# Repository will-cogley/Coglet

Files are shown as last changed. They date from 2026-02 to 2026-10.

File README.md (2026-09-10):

# Coglet
Will Cogley's DIY Desktop Companion for Makers. Support our kickstarter to allow us to keep improving Coglet and so we can offer all components in one place! https://www.kickstarter.com/projects/willcogley/coglet-open-source-3d-printable-robot-companion-kit

# Instructions
*Core documentation for the system and PCB can be found in the [CogNog Datasheet](https://github.com/will-cogley/Coglet/blob/main/CogNogDatasheet.md)*

Refer to the [build video](https://www.youtube.com/watch?v=-7I-jFSNP2E). 

For further reading and troubleshooting, refer to the translated docs in this repo.

# Parts List
Consider backing our [kickstarter](https://www.kickstarter.com/projects/willcogley/coglet-open-source-3d-printable-robot-companion-kit) so we can provide all the parts in [one place!](https://nmrobots.com/)
- CogNog PCB - See project files
- [Grove Vision AI V2 plus camera and adaptor](https://nmrobots.com/products/grove-vision-ai-module-v2-hd-camera-adaptor-15-pin-flex-cable)
- [Microphone](https://www.amazon.co.uk/EC-Buying-INMP441-Omnidirectional-Microphone/dp/B0C1C64R8S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)
- [6 Pin PicoBlade Connector](https://thepihut.com/products/1-25mm-pitch-6-pin-cable-20cm-long-1-1-cable-molex-picoblade-compatible)
- [Speaker](https://www.aliexpress.com/item/1005008267342362.html?spm=a2g0o.order_list.order_list_main.5.2c9d1802tZvBqq)
- USB input to JST XH (3A recommended)
- [ESP Camera - OV3660](https://www.aliexpress.com/item/1005007456084280.html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)
- [ESP Cam Ribbon Cable](https://www.digikey.co.uk/en/products/detail/gct/05-24-A-0152-A-4-06-4-T/21266890)
- [ESP Cam Adaptor](https://www.digikey.co.uk/en/products/detail/adafruit-industries-llc/4524/12323567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)
- [9x Servos - These are tight, MG90s may also work](https://uk.robotshop.com/products/kpower-9g-analog-metal-gear-rc-servo-m0090)
- [Realistic Camera-Compatible Eyes](https://nmrobots.com/products/ultra-realistic-eyeball-compatible-with-face-tracking-eyemech-%CE%B53-4)

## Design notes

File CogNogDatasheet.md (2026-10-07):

# 1. Hardware

## 1.1 Description

A dual-MCU animatronics and AI processing platform combining an ESP32-S3 for machine learning/vision/audio and an RP2040 for real-time kinematics and servo control.

### 1.1.1 Key Features

- **Main Processor:** ESP32-S3 (Wi-Fi/BLE, AI acceleration, I/O)
- **Coprocessor:** RP2040 (Real-time I/O, motion profiling)
- **Motor Control:** PCA9685 16-channel PWM driver
- **Vision:** DVP Camera interface (supports GC0308)
- **Audio:** I2S Microphone input and I2S Speaker amplifier
- **Power:** Single USB-C power input for up to 12 servos

---

## 2. System Block Diagram



---

## 3. Pinout



### 3.1 Default Servo Wiring

| Named Servo | Key in Code | Socket Number (Also PCA9685 Pin No.) |
| --- | --- | --- |
| Right Ear | "EAR" | 0 |
| Left Ear | "EAL" | 1 |
| Eyelid | "LID" | 2 |
| Mouth | "MOU" | 3 |
| Right Eye | "EYR" | 5 |
| Left Eye | "EYL" | 4 |
| Neck Pitch | "PIT" | 8 |
| Neck Roll | "ROL" | 9 |
| Base Yaw | "YAW" | 10 |

---

## 4. Components

### 4.1 On-Board Components

| Name | Function | Interface | Datasheet |
| --- | --- | --- | --- |
| ESP32-S3 | Wi-Fi/BLE, AI acceleration, I/O | - | https://documentation.espressif.com/esp32-s3_datasheet_en.pdf |
| RP2040 | Real-time I/O, motion profiling | - | https://pip-assets.raspberrypi.com/categories/814-rp2040/documents/RP-008371-DS-1-rp2040-datasheet.pdf |
| MAX98357A | Speaker amplifier | I2S | https://cdn-shop.adafruit.com/product-files/3006/MAX98357A-MAX98357B.pdf |
| PCA9685 | Servo driver | I2C | https://www.futurlec.com/Philips/PCA9685PW.shtml |
| CH343P | USB bus converter chip | UART | https://cdn-learn.adafruit.com/assets/assets/000/134/549/original/CH343DS1.PDF?1737477957 |

### 4.2 Recommended External Components

| Name | Function | Interface | Datasheet | Link | Notes |
| --- | --- | --- | --- | --- | --- |
| GC0308 Camera | In-depth vision processing | DVP | https://download.kamami.pl/p1197045-GC0308.pdf | - | **Coglet uses a customised camera with inverted pin layout!** |
| Grove Vision AI Module | Processes face tracking  | UART | https://wiki.seeedstudio.com/Grove-Vision-AI-Module/ | https://nmrobots.com/products/grove-vision-ai-module-v2-hd-camera-adaptor-15-pin-flex-cable |  |
| OV5647 Camera | Realtime face tracking | DVP | - | https://nmrobots.com/products/grove-vision-ai-module-v2-hd-camera-adaptor-15-pin-flex-cable |  |
| Speaker | Speaking responses out loud | Direct Voltage | - | - |  |
| Microphone | Recording audio, listening for responses | I2S | - | - |  |
| Servos | Driving the robot | PWM | - | https://nmrobots.com/products/tiankongrc-ts90md-micro-servo-motor-with-metal-gears |  |

## 5. Power Ratings

*Stresses beyond these limits may cause permanent damage to the board.* 

| Parameter | Symbol | Typical Voltage $V$ | Typical Current $A$ |
| --- | --- | --- | --- |
| **Main Input** | **$V_{IN}$** | **5.0** | **3.0** |
| ESP32 Logic Input  | $V_{LOGIC\_ESP}$ | 3.3 | 0.04 |
| RP2040Logic Input  | $V_{LOGIC\_RP}$ | 3.3 | 0.012 |
| Servo Output Voltage | $V_{IN\_SERVO}$ | 5.0 | 3.0 |

---

## 6. Dual-MCU Communication Protocol

ESP32-s3 sends commands to the RP2040 via UART in the form of simple strings which correspond to preset animations:

$ESP-RX_{GPIO18} : RP2040-TX1_{GPIO04}$

$ESP-TX_{GPIO17} : RP2040-RX1_{GPIO05}$

---

## 7. Power Architecture

Power is provided to the board via the connector in the bottom left corner using a JST-XH connector. This input powers both MCUs via 3V3 LDOs, and the servos via an isolated 5V line. 

**It is required to use a 5V-3A rated power supply**(eg - a USB charger with 5V-3A power rating). If using the Coglet USB > JST XH adaptor, must use a USBA > USBC cable. 

The system can be powered via the programming port, but no power will be delivered to the servos (this approach can be helpful when debugging/developing on the ESP32)

---

## 8. Mechanical Specifications

- **Dimensions:** 72 mm x 81 mm
- **Mounting Holes:** 4 x 2.75mm (to suit M2.5 screws)
- **PCB Layers:** 4



---

## 9. Downloads

*Refer to GitHub root for open-source files such as schematic, layout, STEP, etc*

---

# 2. Software & Firmware

### 2.1 Overview

- Toolchain: ESP-IDF, C++, Python
- Key Libraries: XiaoZhi AI Open-Source Chatbot: https://github.com/78/xiaozhi-esp32

*FAQ: Is it essential to use XiaoZhi AI?  The system is a helpful starting point to get up and running quickly, but for developers it is not necessary. NMRobotics is also developing a locally-running alternative dashboard.* 

## 2.2 Default Functionality

| Item | Functionality |
| --- | --- |
| Programming Selector Switch | Use to switch which MCU is connected to the programming port USB - enabling you to program both MCUs with the same port |
| Calibration Mode Switch | Via the RP2040, put all servos into a default position to assist with making sure all servos are properly calibrated when assembling |
| Facetrack Mode Switch | Via the Grove Vision AI Board, track and follow user’s face in realtime (uses on-board local processing) |
| Servo Test Button  | Via the RP2040, simultaneously wiggle all servos back and forth by a few degrees to check ROM and function during assembly/testing |

## 2.3 Guides

*This section is a stub ! Most recent tutorial overview can be found here:*

https://youtu.be/-7I-jFSNP2E?si=6lqtyZIJ3J-2O9Dj

### 2.3.1 Manually Uploading Code

1. It is recommended to follow this guide to setup ESP-IDF: https://github.com/will-cogley/Coglet/blob/main/Translated Docs for XiaoZhi AI/Setting up the ESP IDF 5.5.2 Development Environment on Windows and Compiling Xiaozhi - Feishu Docs.pdf
2. Clone the github repository 
3. Using ESP-IDF, build and flash 

### 2.3.2 Adding a customised wakeword

1. coming soon

---

# 3. Troubleshooting

| Issue | Recommended action |
| --- | --- |
| "Images taken with camera are over/under exposed | Search in "main\boards\common\ esp32_camera. cc " for: {0xd3, 0xb0} Then change it to: {0xd3, 0x70}, If you think the light is too dim, change "0x70" to "0x78". Re-build and flash the code via ESP-IDF" |
| No power to main board when using USBC > JST XH adaptor board | Use a power adaptor featuring a USBA > USBC cable |

---

# 4. Revision History

| Revision | Date | Description | Author |
| --- | --- | --- | --- |
| V1.0 | 2025-12-02 | Initial prototype  | Will Cogley |
| V1.1 | 2026-01-07 | Minor tweaks  | Will Cogley |
| V2.0 | 2026-06-01 | First Production Prototype | Spike |
| V2.1 | 2026-07-02 | Alternative Production Prototype | Petr Dvorak |
| V2.2 | 2026-08-01 | Minor tweaks from Petr’s design | Xiao Zou |
| V3.0 | 2026-09-06 | Finalised production design for batch 01 | Xiao Zou, Will Cogley |

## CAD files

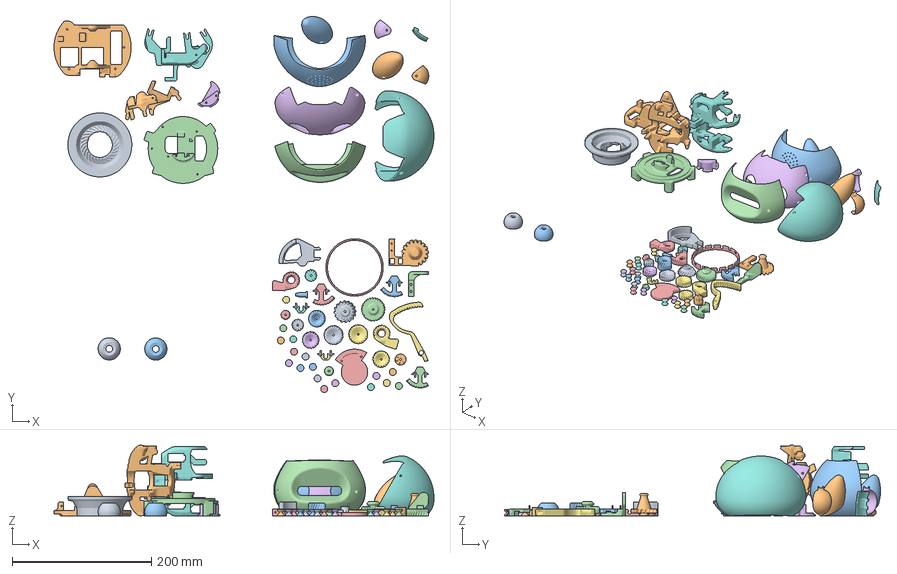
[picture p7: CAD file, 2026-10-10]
3D Printing Files/CogletC0_6_4.3mf
546.3 x 540.6 x 101.7 mm
Full.stl_32 x 2
Full (5).stl_1
Full (5).stl_2
Full.stl_35
Full.stl_48
Full.stl_58
Full.stl_20
Full.stl_8
Full.stl_19
Full.stl_31
Exterior - Eyelid.stl
Full.stl_26 x 2
Full.stl_30
Full.stl_38
Full.stl_16
Full.stl_65
Full.stl_64
Full.stl_29
Full.stl_25
Full - BottomPlug.stl
Full.stl_18
Full.stl_7
Full.stl_22
Full - Part 24.stl
Full.stl_9
Full - BodyMiddlePlatform.stl
Full (4).stl_1
Full.stl_53
Full.stl_57
Full (3).stl_2
Full (3).stl_1
Full.stl_2
Full.stl_24
HeadMech - EarLock.stl x 2
Full.stl_10 x 17
Full - EyeAdaptorR.stl x 2
Full - Foot (1).stl
Full - BodyTopPlatform (4).stl
Full (6).stl_1
Full (6).stl_2

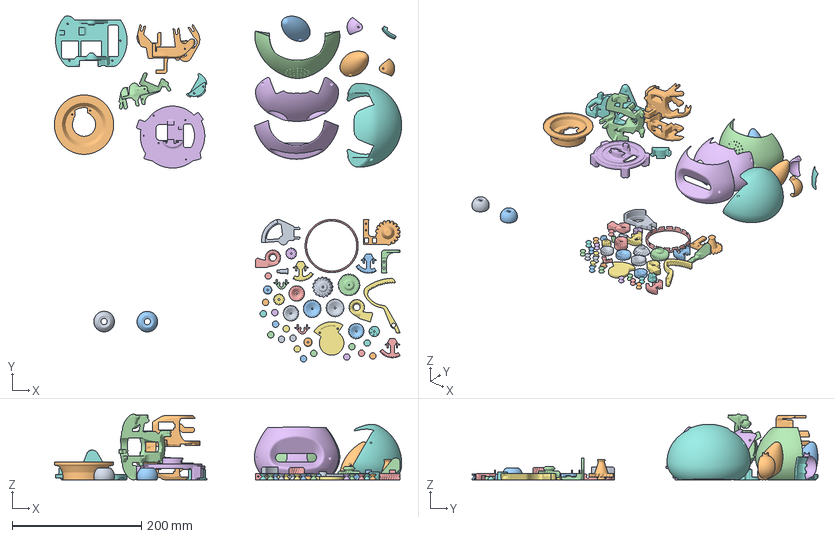
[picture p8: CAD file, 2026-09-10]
3D Printing Files/CogletC0_4.3mf
538.3 x 536.3 x 101.7 mm
Full.stl_32 x 2
Full (5).stl_1
Full (5).stl_2
Full.stl_35
Full.stl_48
Full.stl_58
Full.stl_20
Full.stl_8
Full.stl_19
Full.stl_31
Exterior - Eyelid.stl
Full.stl_26 x 2
Full.stl_30
Full.stl_38
Full.stl_16
Full.stl_65
Full.stl_64
Full.stl_52
Full.stl_29
Full.stl_45
Full.stl_25
Full - BottomPlug.stl
Full.stl_18
Full.stl_7
Full.stl_22
Full - Part 24.stl
Full.stl_9
Full - BodyMiddlePlatform.stl
Full (4).stl_1
Full - BodyTopPlatform.stl
Full.stl_53
Full - Foot.stl
Full.stl_57
Full.stl_47
Full.stl_44
Full (3).stl_2
Full (3).stl_1
Full.stl_2
Full.stl_24
HeadMech - EarLock.stl x 2
Full.stl_10 x 17

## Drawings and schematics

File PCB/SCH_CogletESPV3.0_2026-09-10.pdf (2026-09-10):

# ESP32-S3 N16R8

# Key

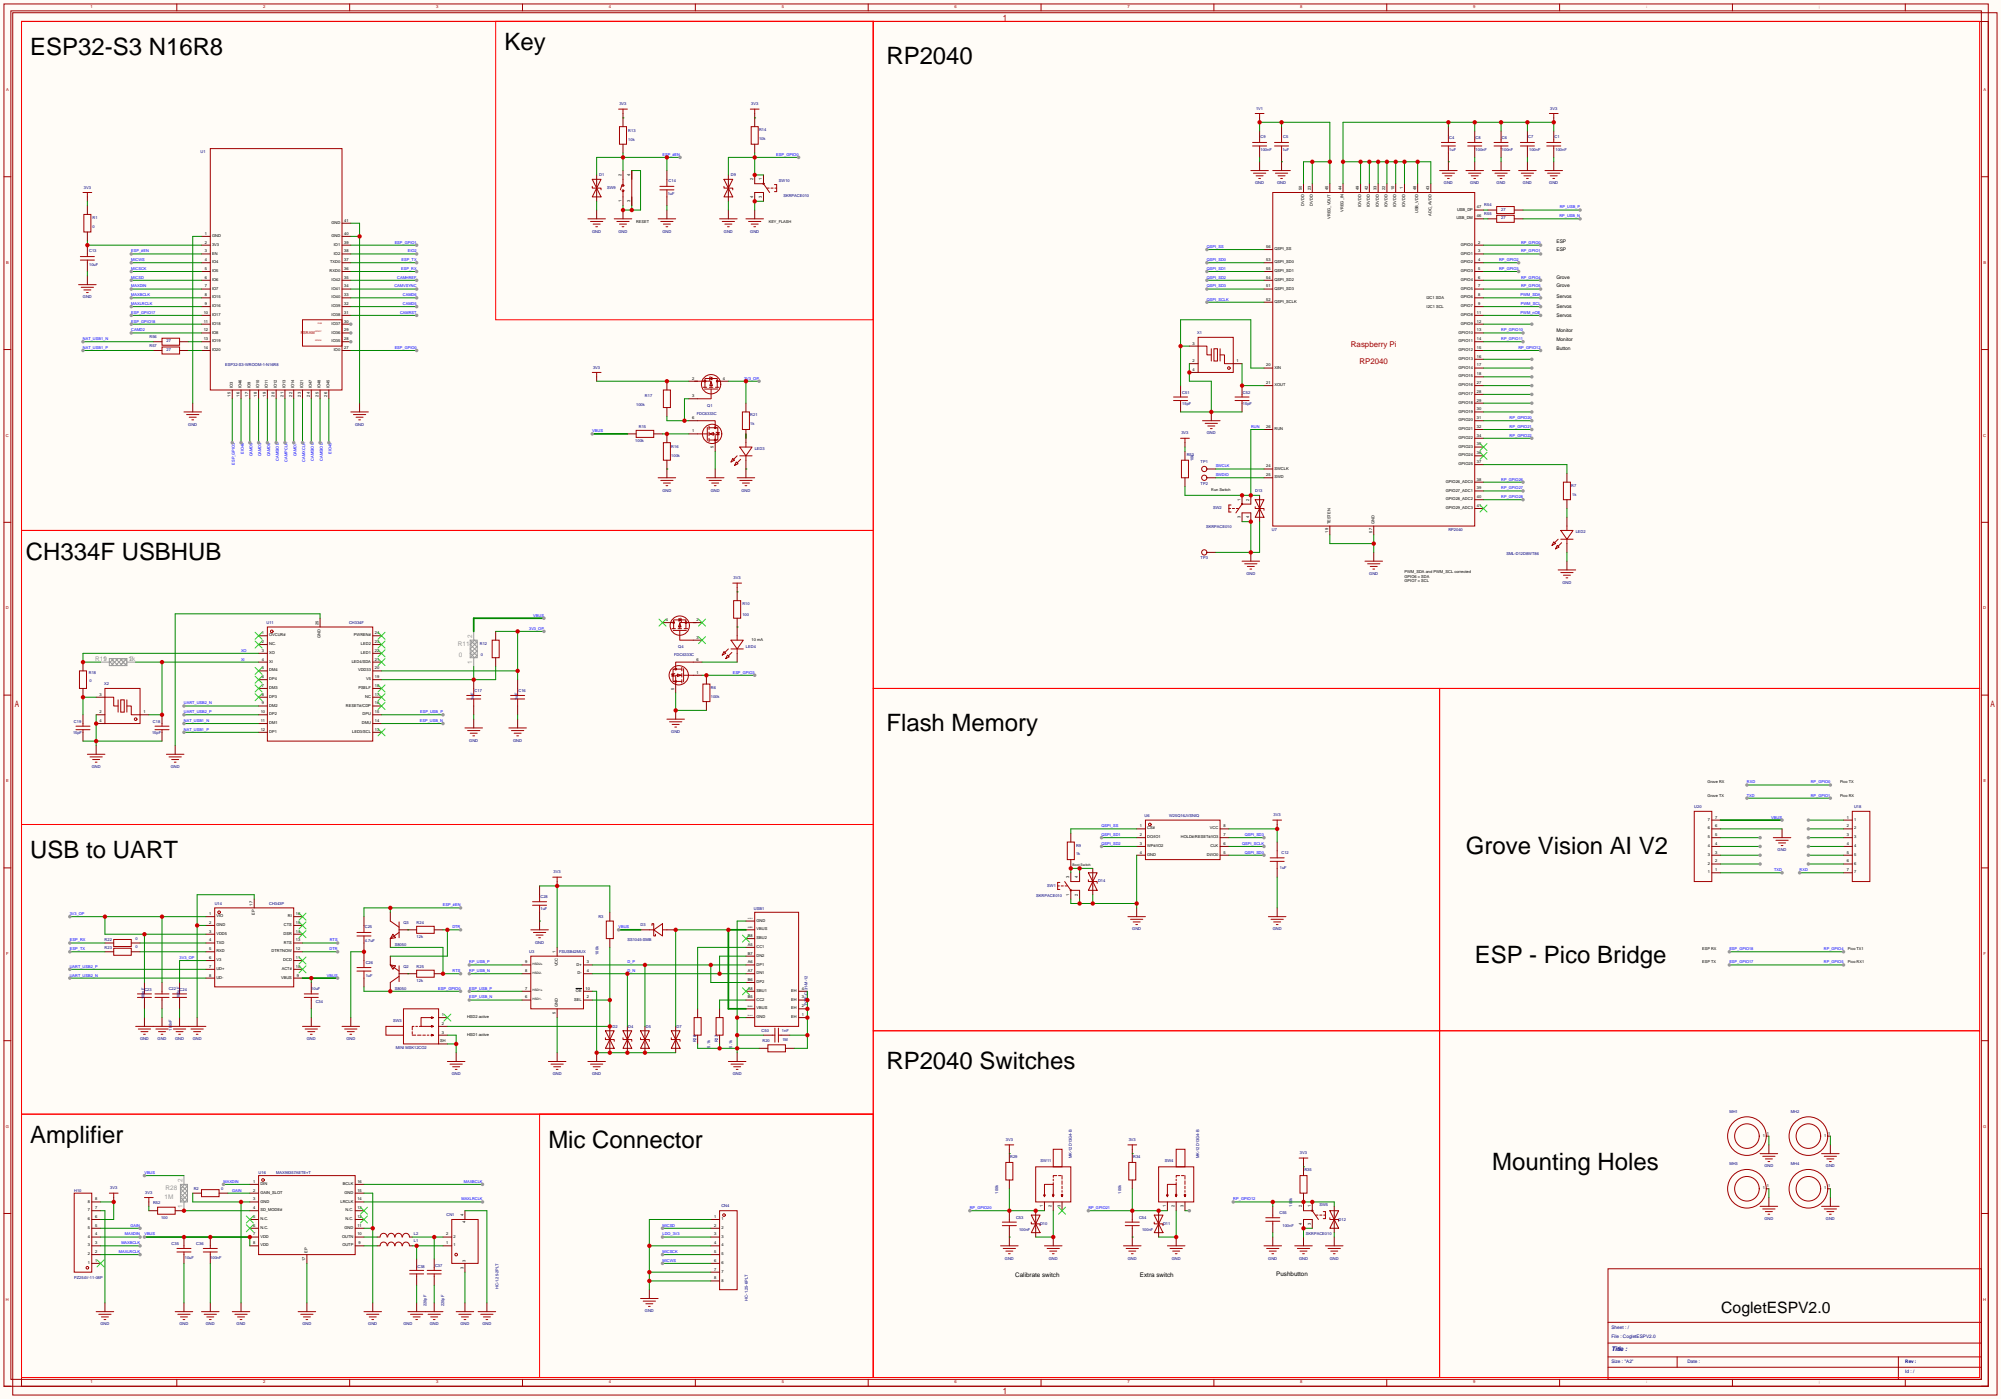
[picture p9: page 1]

Main Power | 3V3 LDO

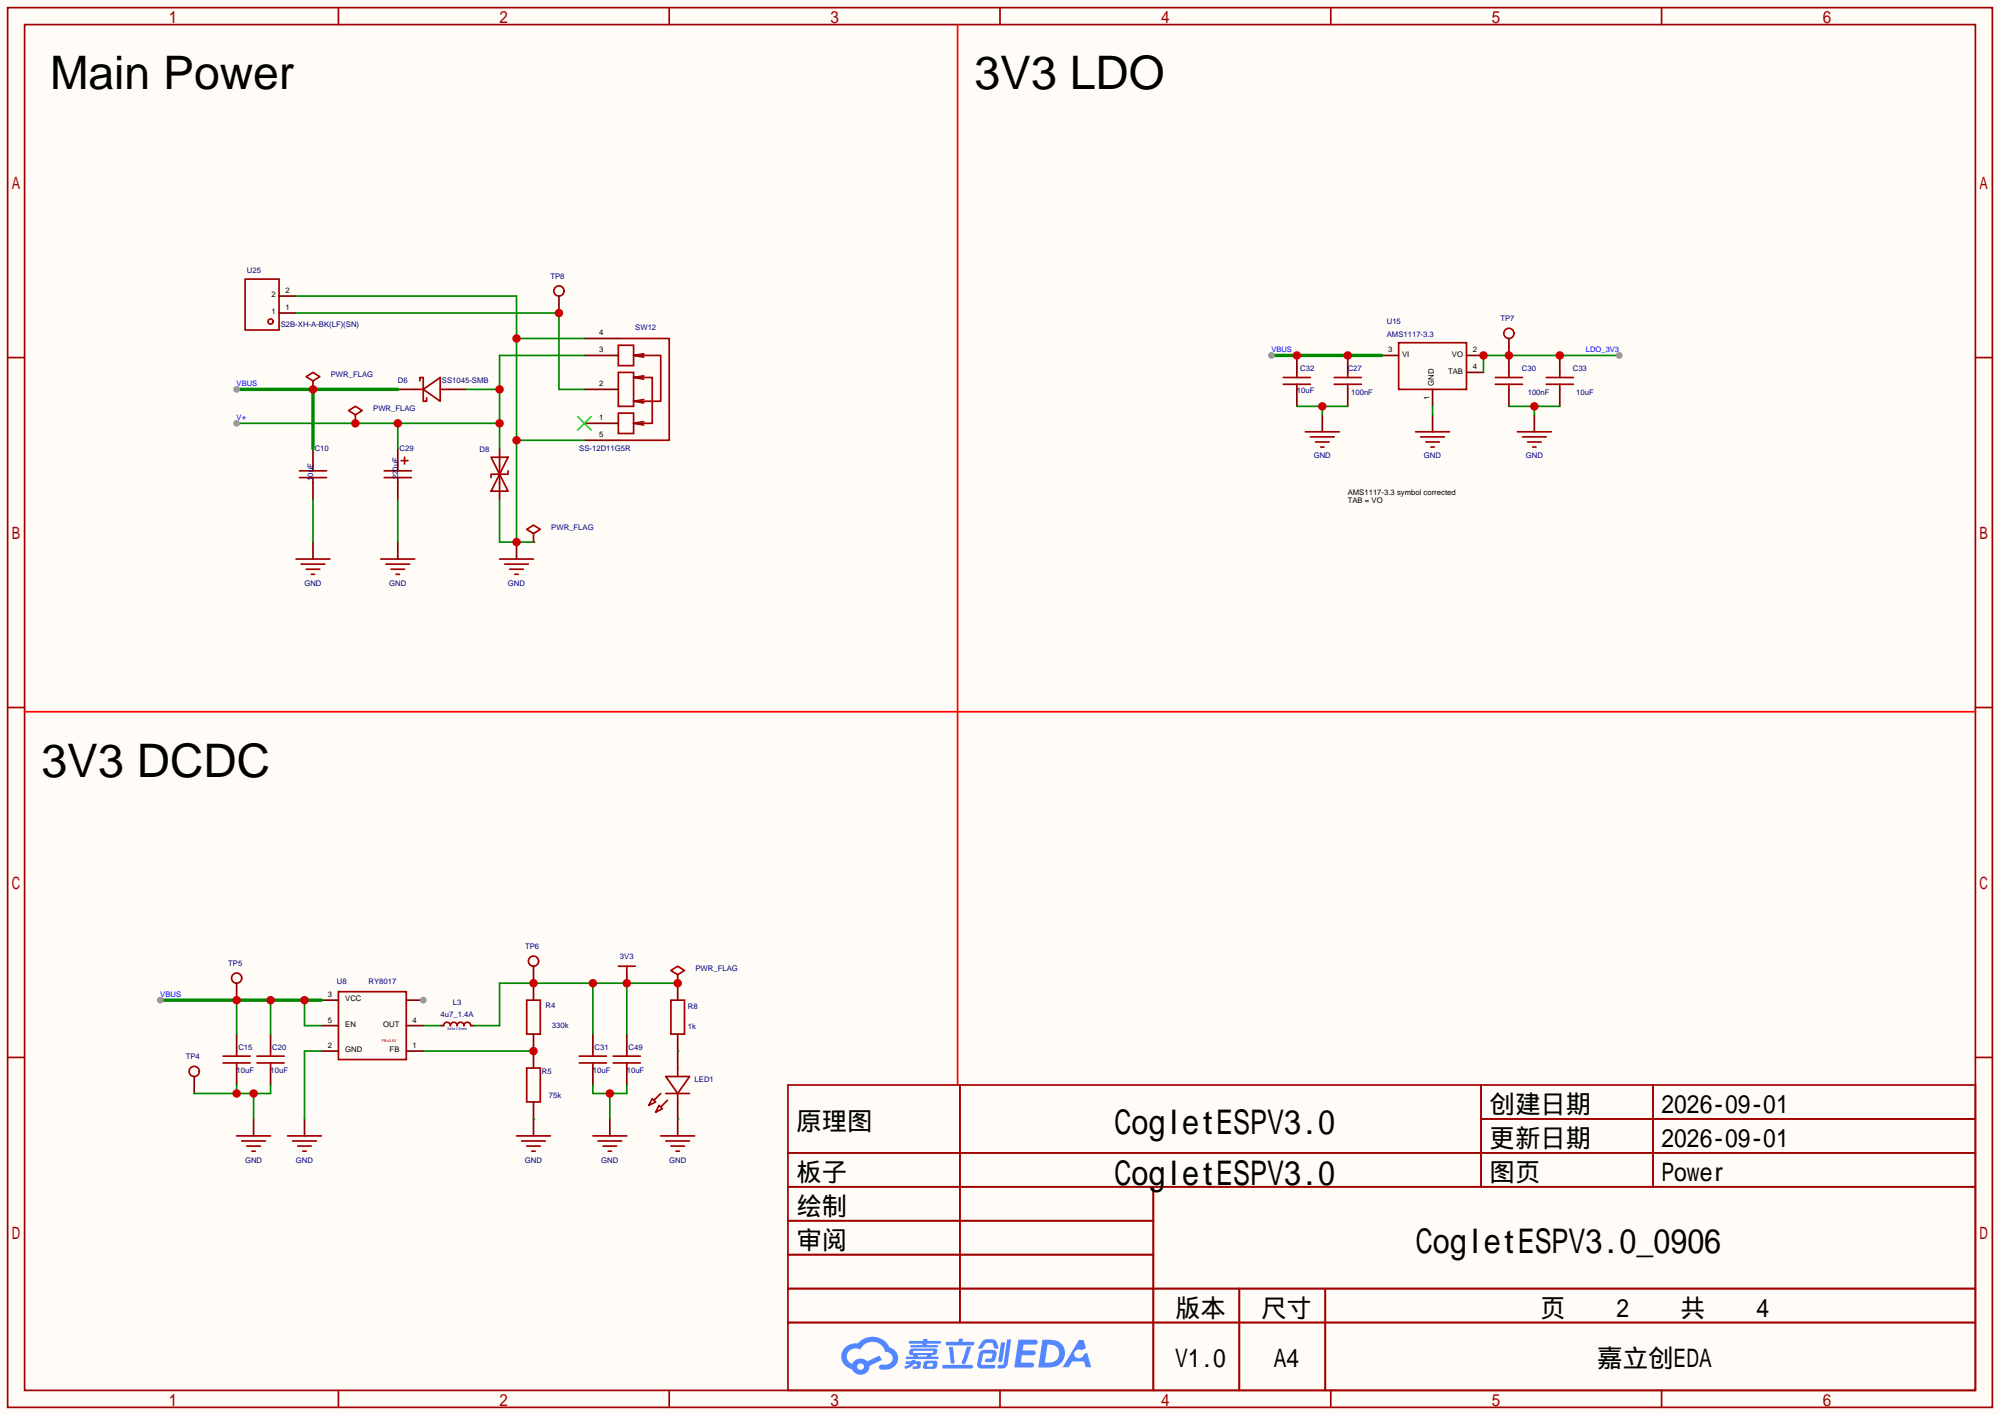
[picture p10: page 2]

原理图 | CogletESPV3.0 | 创建日期 | 2026-09-01
板子 | CogletESPV3.0 | 图页 | Power
绘制 | | CogletESPV3.0_0906
审阅

更新日期 | 2026-09-01

V1.0 | A4 | 嘉立创EDA

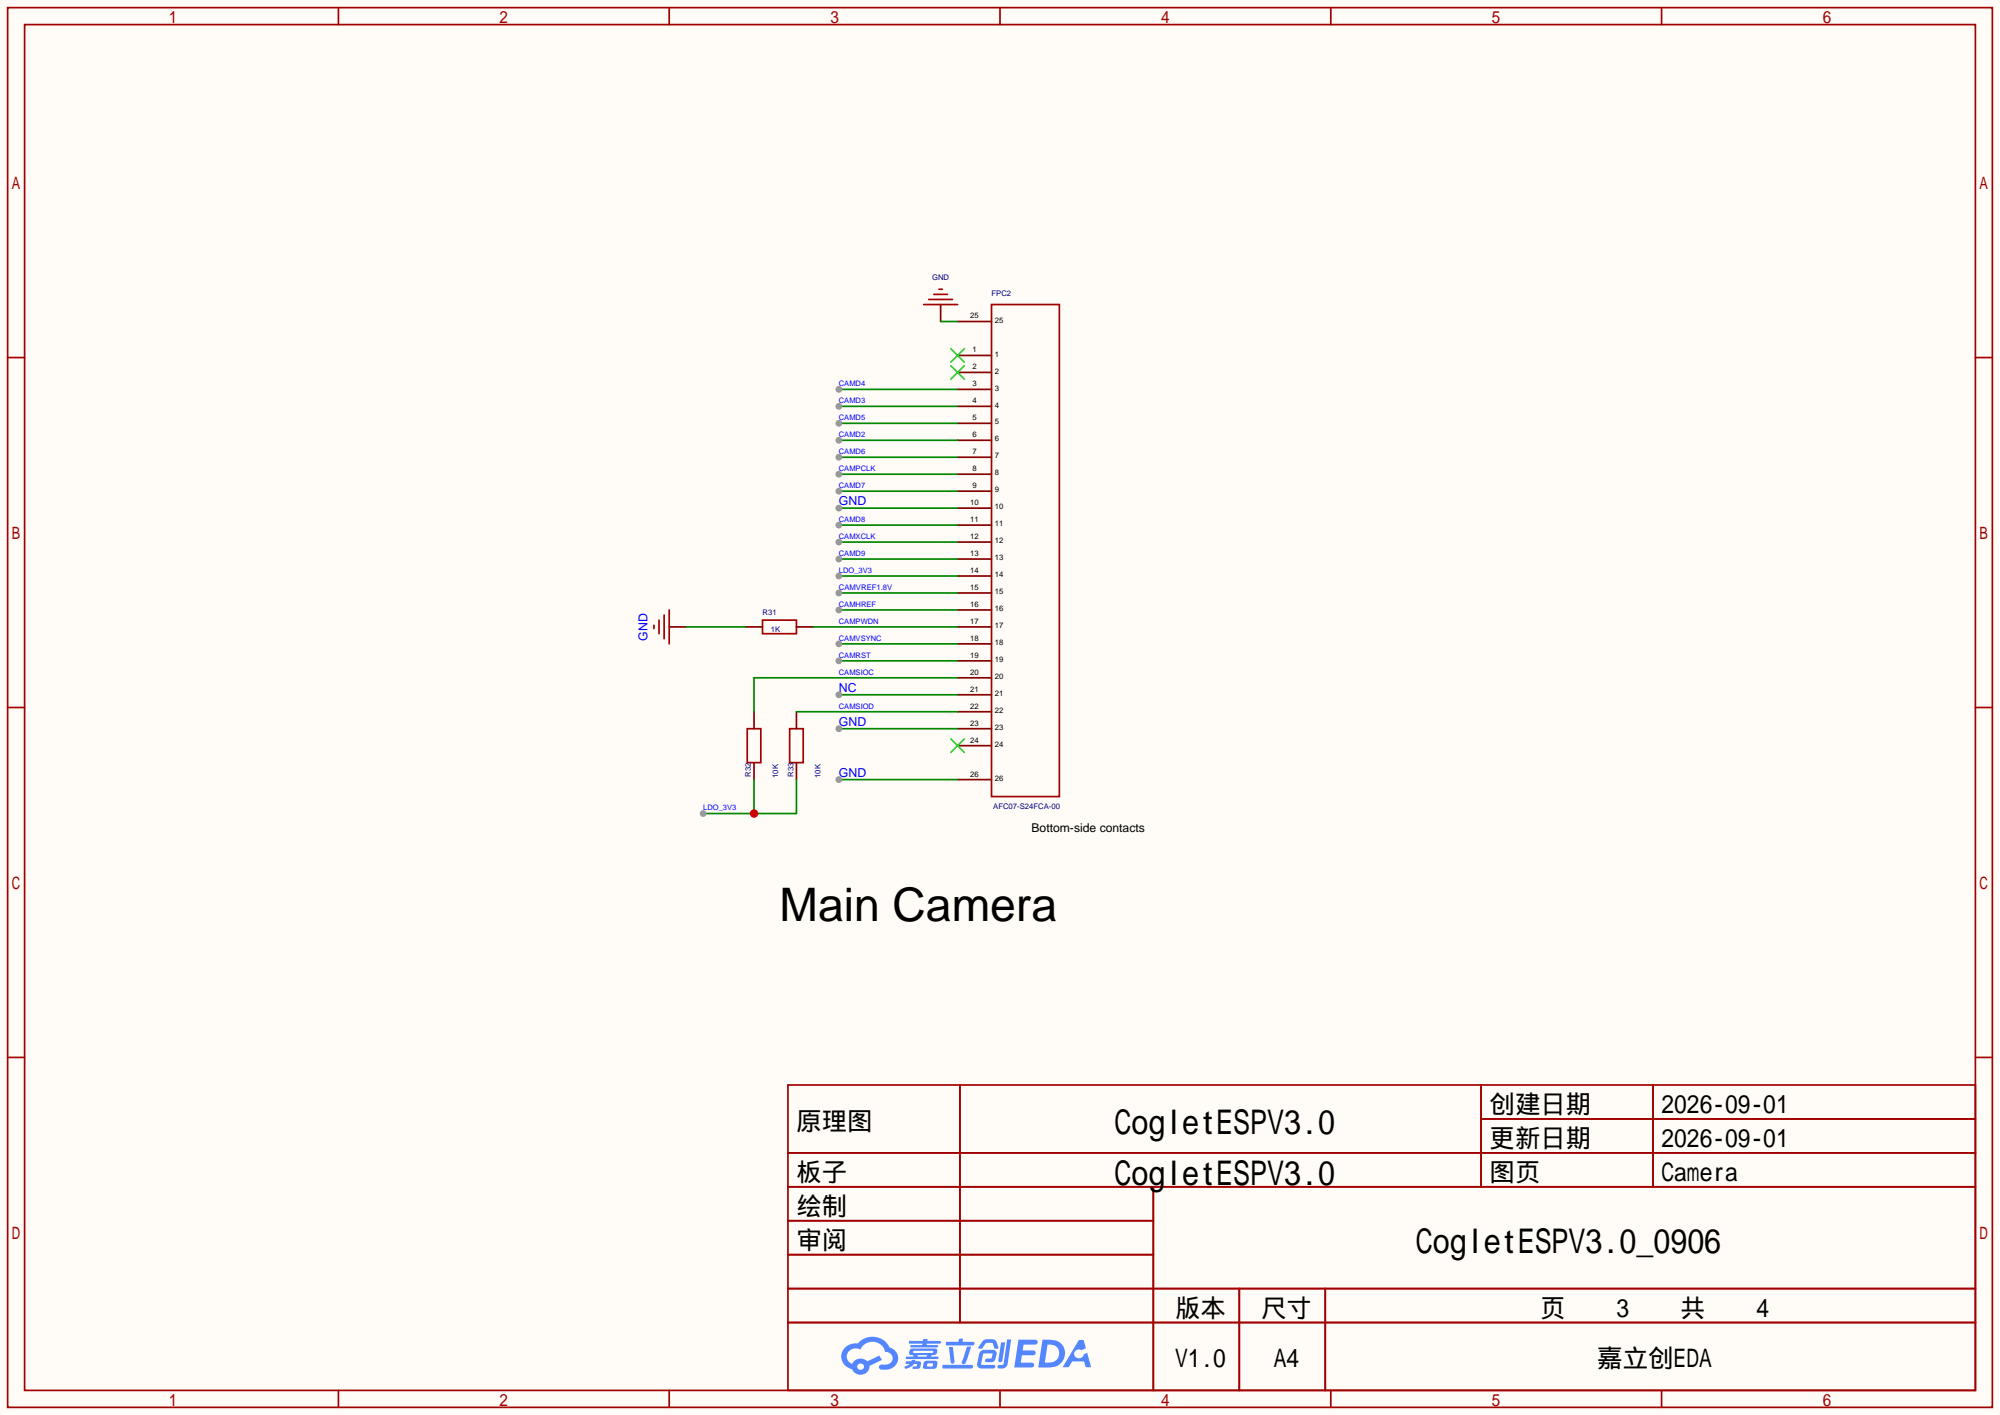
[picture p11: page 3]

原理图 | CogletESPV3.0 | 创建日期 | 2026-09-01
板子 | CogletESPV3.0 | 图页 | Camera
绘制 | | CogletESPV3.0_0906
审阅

更新日期 | 2026-09-01

Servos | HX

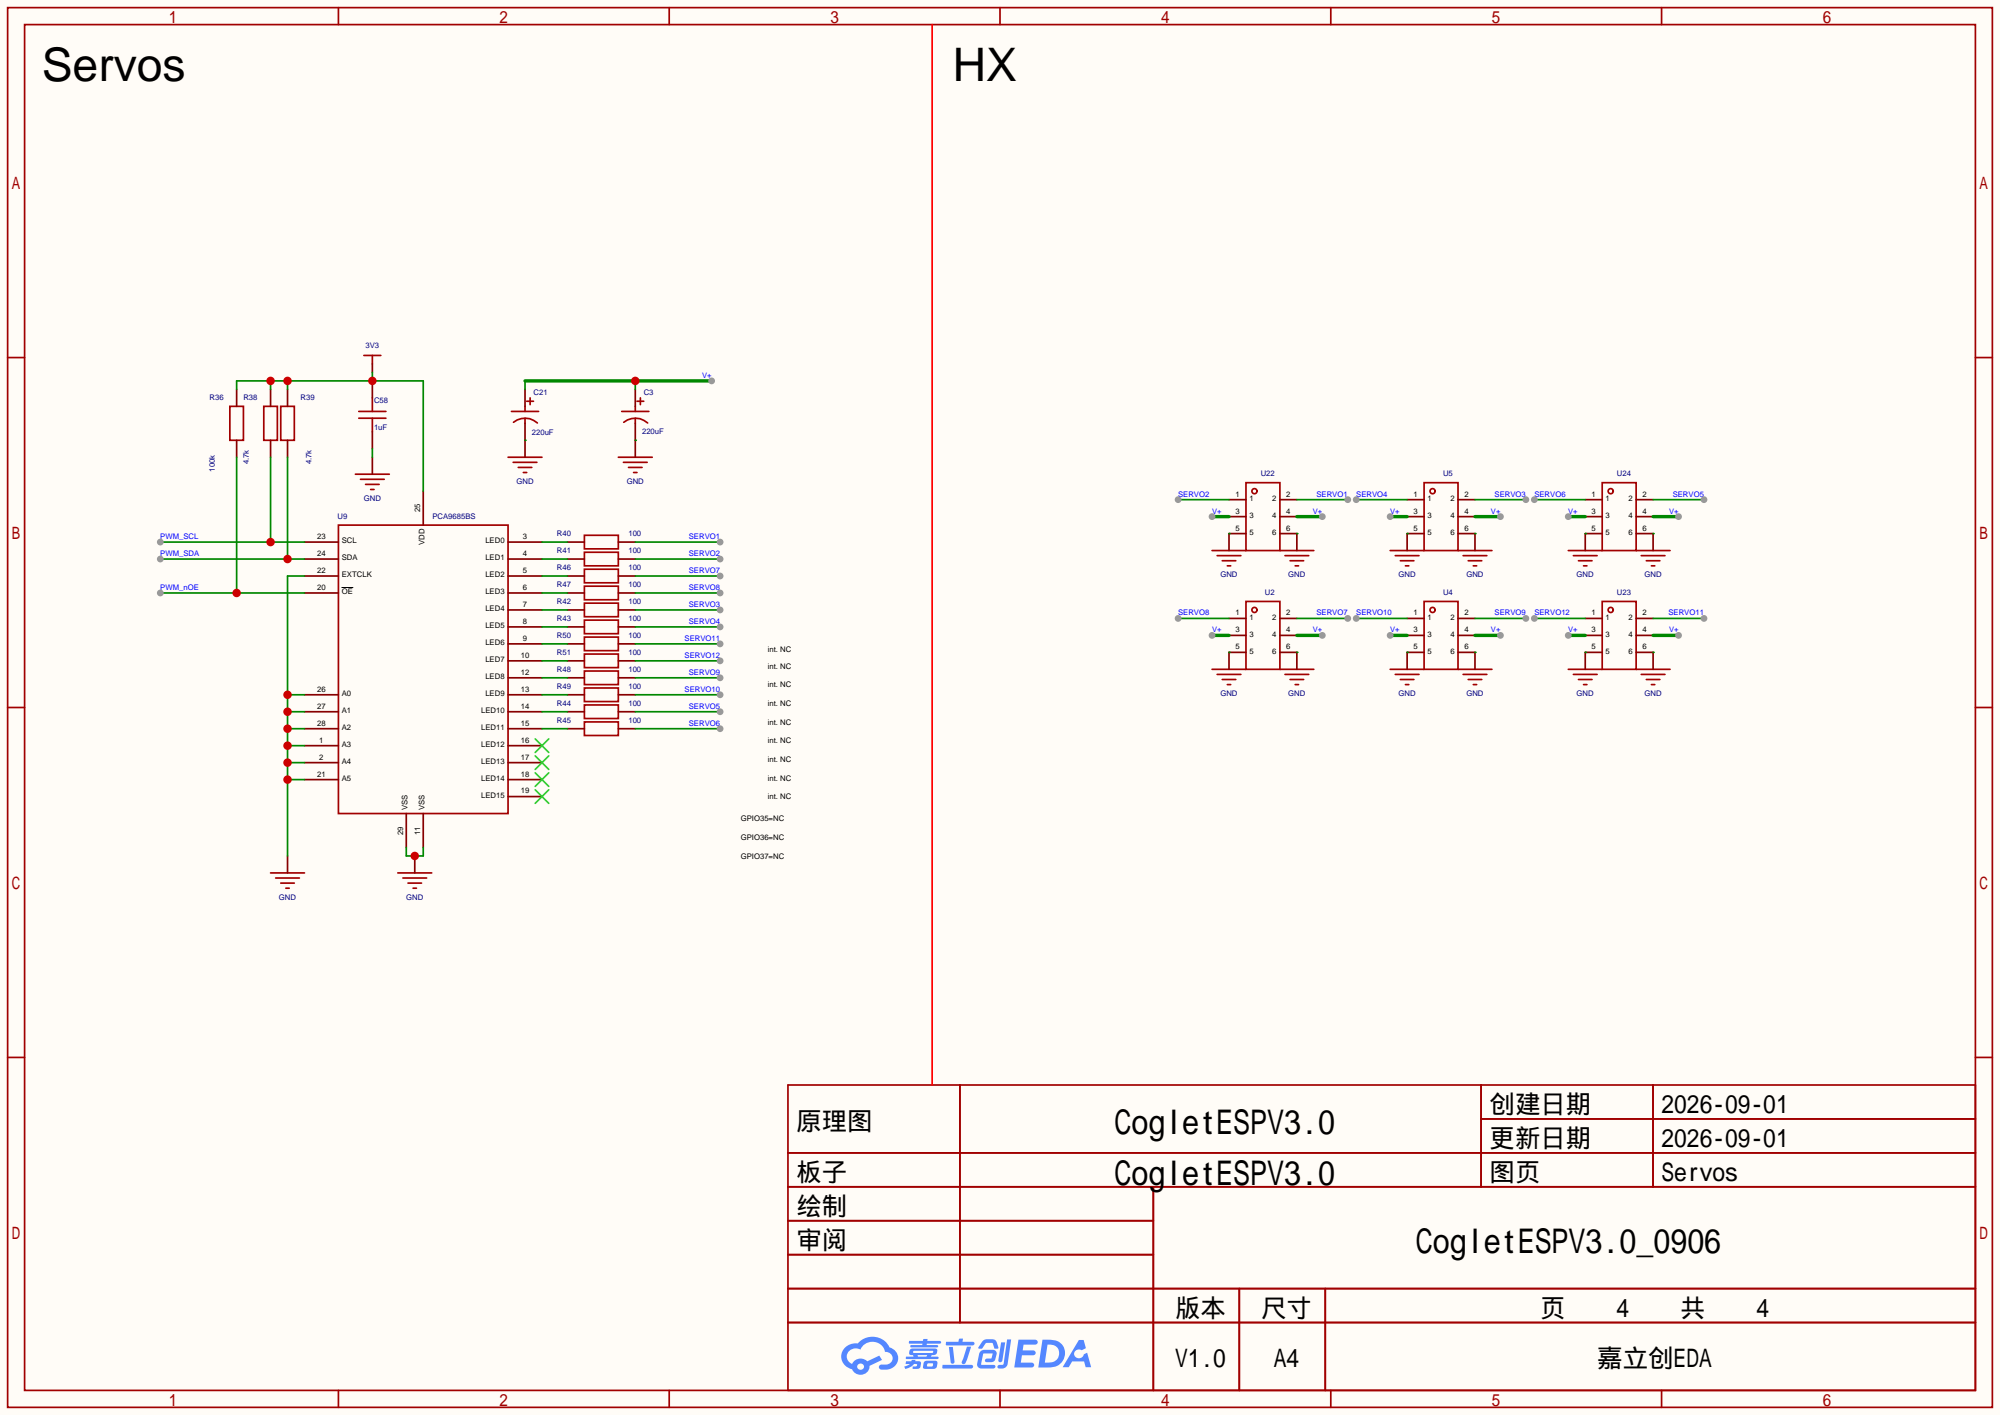
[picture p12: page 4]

原理图 | CogletESPV3.0 | 创建日期 | 2026-09-01
板子 | CogletESPV3.0 | 图页 | Servos
绘制 | | CogletESPV3.0_0906
审阅

更新日期 | 2026-09-01

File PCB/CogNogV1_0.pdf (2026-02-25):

IO0 27 IO35 28 IO36 29 IO37 30 IO38 31 IO39 32 IO40 33 IO41 34 IO42 35 RXD0 36 TXD0 37 IO2 38 IO1 39 GND 40

# QSPI_SD3 51 DVDD ⁵⁰

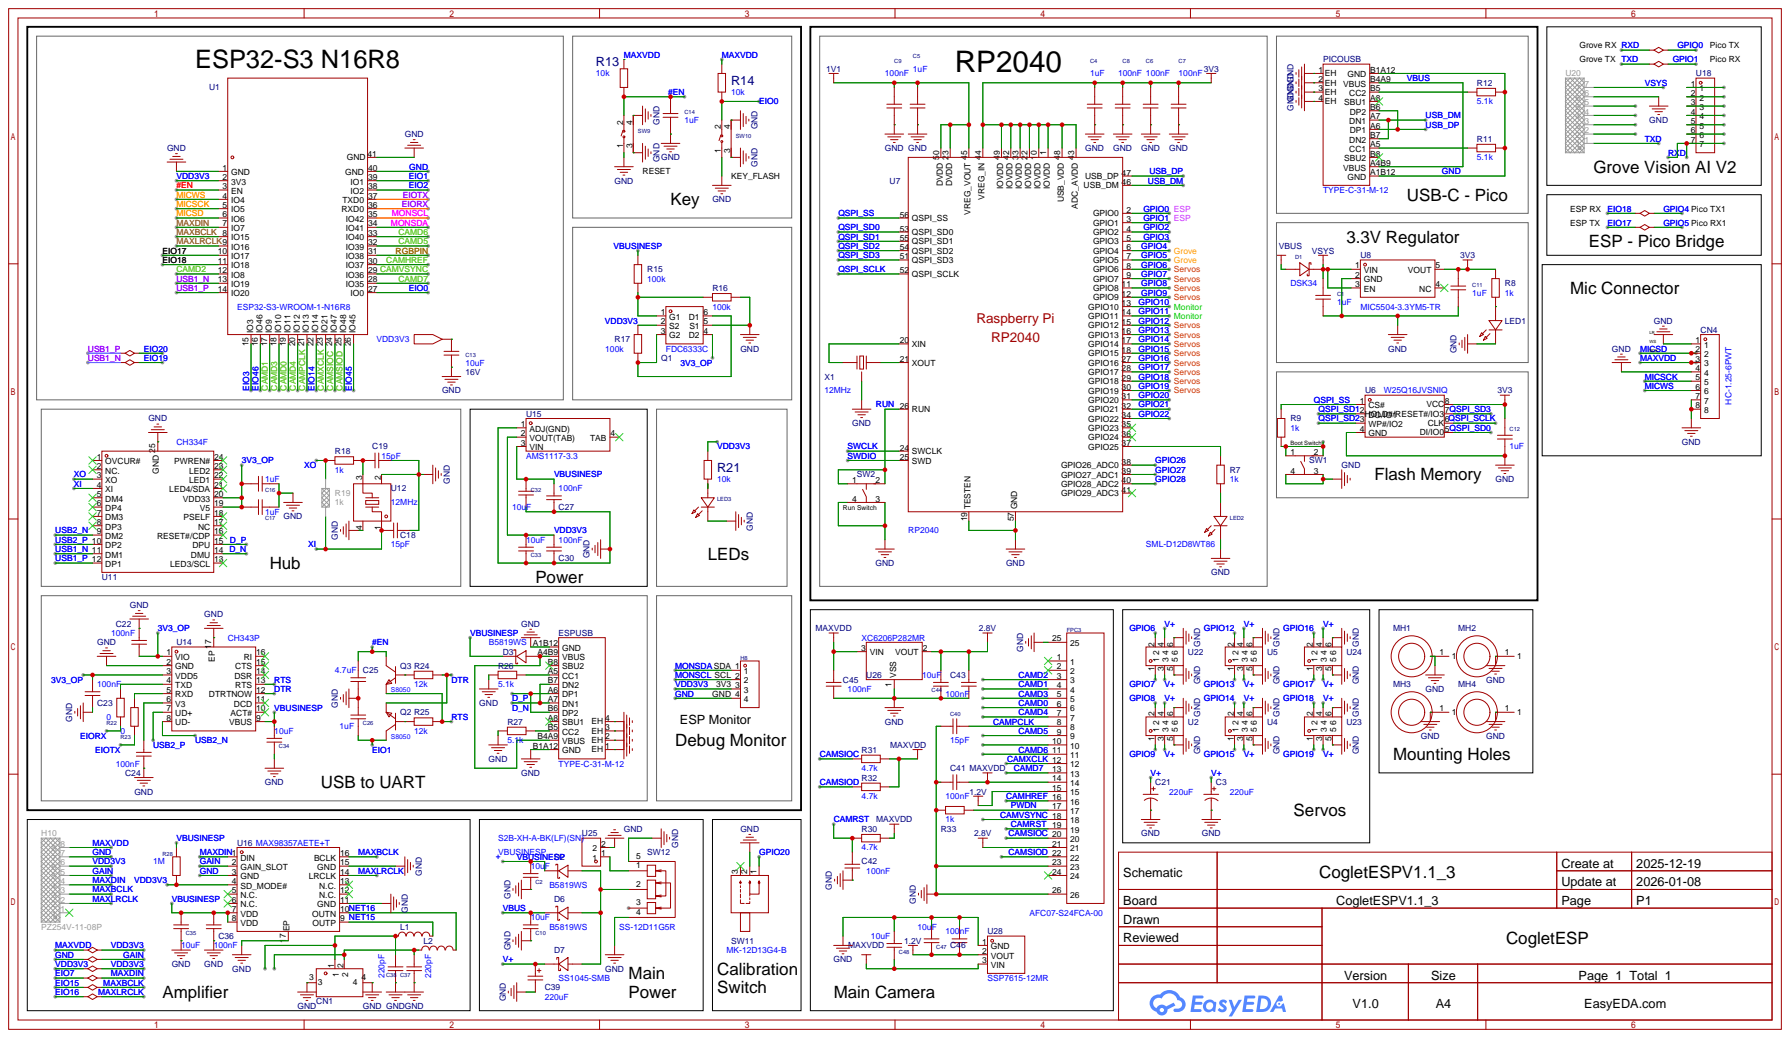
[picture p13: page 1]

GND GND

ACT# 10 DCD 11 DTRTNOW 12 RTS 13 DSR 14 CTS 15 RI 16 EP ¹⁷

OUTN 10 GND 11 N.C. 12 N.C. 13 LRCLK 14 GND 15 BCLK 16

Schematic | CogletESPV1.1_3 | Create at | 2025-12-19

Update at | 2026-01-08

Board | CogletESPV1.1_3 | Page | P1

Version | Size | Page 1 Total 1
V1.0 | A4 | EasyEDA.com

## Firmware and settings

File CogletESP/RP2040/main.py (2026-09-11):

# motion_servo.py  (MicroPython for RP2040)
from machine import Pin, UART
import time, random
import urandom
import servoclass
from servoclass import Servo
import sys, select, uselect
import math
import animation
from animation import servos
from vision import EyeFollower

ESP = UART(1, baudrate=115200, tx=Pin(4), rx=Pin(5))
rx_buffer = b""

# ============================================================
# CogNog / Coglet PCB V2.0 physical controls
# ============================================================
CALIBRATE_PIN = 20
FACETRACK_TOGGLE_PIN = 21
WIGGLE_PIN = 12
FRONT_LED_PIN = 25

calibrate_bool = False
last_toggle = 0


# V2 controls are active LOW.
mode = Pin(CALIBRATE_PIN, Pin.IN, Pin.PULL_UP)
facetrack_toggle = Pin(FACETRACK_TOGGLE_PIN, Pin.IN, Pin.PULL_UP)
wiggle_button = Pin(WIGGLE_PIN, Pin.IN, Pin.PULL_UP)
front_LED = Pin(25, Pin.OUT)

FACETRACK_ON_LEVEL = 0
facetrack_enabled_prev = None

# XiaoZhi device speech activity is tracked separately from emotion.
# Emotions such as "sad"/"happy" must NOT stop the mouth animation.
speech_active = False

# These device states explicitly mean the assistant is no longer speaking.
SPEECH_STOP_SIGNALS = (
    "neutral",
    "idle",
    "listening",
    "thinking",
    "state_startup",
)

# Calibration wiggle:
#   - only runs while Calibration Mode is active AND GPIO12 is held
#   - commands +/-10 degrees around pose_calibrate
#   - non-blocking; PCA updates are limited to 50 Hz
#   - release immediately commands every active servo back to home
WIGGLE_AMPLITUDE_DEG = 10.0
WIGGLE_PERIOD_MS = 1200
WIGGLE_UPDATE_MS = 20

calibration_active_prev = False
wiggle_active_prev = False
wiggle_started_at = time.ticks_ms()
last_wiggle_update = time.ticks_ms()

# Filled from animation.pose_calibrate after PCA/Servo objects exist.
calibration_home = {}


def _clamp(value, low, high):
    if value < low:
        return low
    if value > high:
        return high
    return value


def _refresh_calibration_home():
    """
    Build the diagnostic center position from the project's existing
    pose_calibrate values.

    This deliberately does not invent a second calibration table.
    If pose_calibrate is changed later, the wiggle center follows it.
    """
    calibration_home.clear()

    for name, servo in servos.items():
        raw_home = animation.pose_calibrate.get(name, servo.target)
        safe_home = _clamp(
            float(raw_home),
            float(servo.min_angle),
            float(servo.max_angle),
        )
        calibration_home[name] = safe_home

        low_room = safe_home - float(servo.min_angle)
        high_room = float(servo.max_angle) - safe_home

        if (
            low_room < WIGGLE_AMPLITUDE_DEG
            or high_room < WIGGLE_AMPLITUDE_DEG
        ):
            print(
                "[CAL] WARN {} home={} range={}..{} "
                "cannot reach full +/-{} deg; motion will be safety-clamped".format(
                    name,
                    safe_home,
                    servo.min_angle,
                    servo.max_angle,
                    WIGGLE_AMPLITUDE_DEG,
                )
            )


def _command_calibration_home(immediate=False):
    for name, servo in servos.items():
        if not servo.enabled:
            continue

        home = calibration_home[name]

        if immediate:
            servo.set_immediate(home)
        else:
            servo.set_target(home)


def _update_calibration_wiggle(now):
    """
    Return True while calibration owns all servo commands.

    The diagnostic uses a smooth sine command instead of a blocking
    sleep()/while wiggle loop.  This keeps UART, Vision AI servicing,
    and the main loop alive while the button is held.
    """
    global calibration_active_prev
    global wiggle_active_prev
    global wiggle_started_at
    global last_wiggle_update

    calibration_active = (mode.value() == 0)
    wiggle_pressed = (wiggle_button.value() == 0)

    # Enter Calibration Mode: calibration owns the servos.
    if calibration_active and not calibration_active_prev:
        _refresh_calibration_home()
        _command_calibration_home(immediate=False)
        wiggle_active_prev = False
        print("[CAL] ENTER: GPIO20=LOW -> calibration owns servos")

    if calibration_active:
        if wiggle_pressed:
            if not wiggle_active_prev:
                wiggle_started_at = now
                last_wiggle_update = time.ticks_add(
                    now,
                    -WIGGLE_UPDATE_MS,
                )
                print(
                    "[CAL] WIGGLE START: GPIO12=LOW, amplitude=+/-{} deg".format(
                        WIGGLE_AMPLITUDE_DEG
                    )
                )

            if (
                time.ticks_diff(now, last_wiggle_update)
                >= WIGGLE_UPDATE_MS
            ):
                elapsed = time.ticks_diff(now, wiggle_started_at)
                phase = (
                    (elapsed % WIGGLE_PERIOD_MS)
                    * (2.0 * math.pi)
                    / WIGGLE_PERIOD_MS
                )
                offset = WIGGLE_AMPLITUDE_DEG * math.sin(phase)

                for name, servo in servos.items():
                    if not servo.enabled:
                        continue
                    servo.set_immediate(
                        calibration_home[name] + offset
                    )

                last_wiggle_update = now

        else:
            # Exact release path: command the calibrated home immediately.
            if wiggle_active_prev:
                _command_calibration_home(immediate=True)
                print(
                    "[CAL] WIGGLE STOP: GPIO12 released -> "
                    "all active servos HOME"
                )

            # Keep the home target asserted while calibration is active.
            # set_target() does not create extra I2C writes by itself.
            for name, servo in servos.items():
                if servo.enabled:
                    servo.set_target(calibration_home[name])

        wiggle_active_prev = wiggle_pressed

    # Leaving Calibration Mode also terminates any wiggle immediately.
    elif calibration_active_prev:
        if wiggle_active_prev:
            _command_calibration_home(immediate=True)
            print("[CAL] WIGGLE STOP: left Calibration Mode")

        wiggle_active_prev = False

        # The latest XiaoZhi state may have changed while calibration owned
        # the servos. Re-enter it cleanly on this same loop.
        animation.new_state_flag = True
        print("[CAL] EXIT: normal animation/vision control restored")

    calibration_active_prev = calibration_active
    return calibration_active


# Grove Vision AI V2 visual following.
eye_follower = EyeFollower(servos)


def _update_facetrack_toggle():
    """
    GP21 controls ONLY Grove Vision / visual-follow behavior.

    OFF does not suppress XiaoZhi animations and does not move unrelated
    servos.  On the OFF edge, only EYL/EYR/PIT are released to neutral once;
    the normal animation state is then allowed to own any shared axis.
    """
    global facetrack_enabled_prev

    enabled = (facetrack_toggle.value() == FACETRACK_ON_LEVEL)

    if facetrack_enabled_prev is None:
        facetrack_enabled_prev = enabled

        if enabled:
            print("[FACE] GP21 startup: ON -> Grove Vision tracking enabled")
        else:
            eye_follower.release_to_home()
            animation.new_state_flag = True
            print(
                "[FACE] GP21 startup: OFF -> Vision paused; "
                "EYL/EYR/PIT released to neutral"
            )

        return enabled

    if enabled != facetrack_enabled_prev:
        facetrack_enabled_prev = enabled

        if enabled:
            animation.new_state_flag = True
            print(
                "[FACE] SWITCH ON: Grove Vision startup/inference + "
                "visual tracking ENABLED"
            )
        else:
            # Only the three tracking-owned axes are touched.
            eye_follower.release_to_home()

            # Re-enter the current XiaoZhi state once so any legitimate
            # animation ownership (for example PIT in an emotion) can resume.
            animation.new_state_flag = True

            print(
                "[FACE] SWITCH OFF: Grove Vision PAUSED; "
                "EYL/EYR/PIT released; other servos/animations unchanged"
            )

    return enabled


# track direction for each servo (1 = going to max, -1 = going to min)
directions = {name: 1 for name in servos.keys()}

last_time = time.ticks_ms()
last_switch = last_time

# servos["YAW"].set_target(88)
# # servos["RWH"].set_target(89)


print("")
print("==============================================")
print(" Coglet V1 baseline on PCB V2.0")
print(" ESP bridge: UART1 TX=GPIO4 RX=GPIO5 115200")
print(" PCA: SDA=GPIO6 SCL=GPIO7 nOE=GPIO8")
print(" Calibrate: GPIO20 active LOW")
print(" Facetrack: GPIO21 active LOW; controls Grove Vision only")
print(" Wiggle: GPIO12 active LOW, calibration-only +/-10 deg")
print(" Vision: UART0 TX=GPIO0 RX=GPIO1 @ 921600")
print(" Vision control: EYL + EYR only")
print("==============================================")

if not servoclass.is_ready():
    print("[FATAL] PCA9685 0x40 was not detected.")
    print("[FATAL] Servo outputs stay disabled.")
    while True:
        time.sleep_ms(1000)

# Servo objects are created while PCA9685 nOE is HIGH.
# Most channels keep the legacy 90-degree preload, but the eyelid's actual
# startup/calibration position is 110 degrees. Preload that value BEFORE
# enabling nOE so LID does not receive a 90 -> 110 double command at boot.
servos["LID"].set_immediate(animation.pose_calibrate["LID"])
print(
    "[LID] boot preload: {} deg while PWM_nOE is disabled".format(
        animation.pose_calibrate["LID"]
    )
)

servoclass.enable_outputs()

# Build the initial home table once; it is refreshed every time
# Calibration Mode is entered.
_refresh_calibration_home()


while True:
    now = time.ticks_ms()
    dt = time.ticks_diff(now, last_time) / 1000.0
    last_time = now

    if ESP.any():
        rx_buffer += ESP.read()   # bytes + bytes = OK
        while b"\n" in rx_buffer:
            line, rx_buffer = rx_buffer.split(b"\n", 1)
            rcvstate = line.decode().strip()
            print("RX:", rcvstate)

            # Explicit MCP one-shot/temporary actions are a separate UART
            # namespace from normal XiaoZhi expression states.  The RP2040
            # owns the requested action for exactly 2 seconds.
            if rcvstate.startswith("action:"):
                action_name = rcvstate[7:].strip()
                animation.start_mcp_action(action_name, now)
                continue

            # Speech activity and expression are two separate dimensions.
            # "speaking" starts the mouth animation.
            # happy/sad only change expression and leave speech_active untouched.
            # Device states such as neutral/listening/thinking stop speech.
            if rcvstate == "speaking":
                if not speech_active:
                    print("[MOUTH] speech flag: OFF -> ON")
                speech_active = True
            elif rcvstate in SPEECH_STOP_SIGNALS:
                if speech_active:
                    print("[MOUTH] speech flag: ON -> OFF ({})".format(rcvstate))
                speech_active = False

            if rcvstate in animation.state_map:
                # XiaoZhi may report the same state repeatedly during one
                # long TTS response. Do not re-enter the same state, because
                # that would reset the Speaking timers again and again.
                if rcvstate != animation.current_state:
                    print(
                        "state change:",
                        animation.current_state,
                        "->",
                        rcvstate,
                    )
                    # Restore the motion limits declared in animation.servos
                    # before entering a different normal state. This prevents
                    # temporary tuning from excited/silly/shock/etc. leaking
                    # into the next expression.
                    animation.reset_servo_motion_defaults()

                    animation.current_state = rcvstate
                    animation.new_state_flag = True
                else:
                    print("same state ignored:", rcvstate)

    # Calibration retains absolute priority over every servo command.
    # --- START TEMPORARY ANIMATION TEST OVERRIDE ---
    calibration_owns_servos = _update_calibration_wiggle(now)


    if calibration_owns_servos:
        if time.ticks_diff(now, last_toggle) >= 500:
            calibrate_bool = not calibrate_bool   # flip the boolean
            last_toggle = now
        
        # Calibration also pauses new Grove Vision work.
        animation.update_blink(
            now,
            animation.current_state,
            enabled=False,
        )
        eye_follower.update(
            now,
            animation.current_state,
            enabled=False,
        )

    else:
        calibrate_bool = False

        # MCP actions have priority over normal State / Speaking / random Blink
        # / Vision for a fixed 2-second window.  update_mcp_action() returns
        # False on the exact loop where that window expires, so the newest
        # normal state resumes immediately without an extra dead frame.
        mcp_owns_servos = animation.update_mcp_action(now)

        if mcp_owns_servos:
            # Keep background systems alive logically but prevent any of them
            # from issuing competing servo commands during MCP ownership.
            animation.update_blink(
                now,
                animation.current_state,
                enabled=False,
            )
            eye_follower.update(
                now,
                animation.current_state,
                enabled=False,
            )

        else:
            # GP21 affects ONLY Grove Vision / face tracking.
            facetrack_enabled = _update_facetrack_toggle()

            # XiaoZhi animations keep running whether Facetrack is ON or OFF.
            animation.apply_state(animation.current_state)

            animation.update_blink(
                now,
                animation.current_state,
                enabled=True,
            )

            # When GP21 is OFF, vision.py pauses new Vision AI requests and
            # performs no visual-follow servo writes.
            eye_follower.update(
                now,
                animation.current_state,
                enabled=facetrack_enabled,
            )

            # MOU is independent from current emotion.  Run this after all
            # expression/vision updates so speech has final ownership of the mouth.
            animation.update_speaking_mouth(now, speech_active)
        
    front_LED.value(calibrate_bool)

    # During wiggle, set_immediate() writes the PCA command directly.
    # Servo.update() remains safe because pos/target/vel are synchronized
    # by set_immediate(). During non-wiggle calibration it moves toward home.
    for s in servos.values():
        s.update(dt)

    time.sleep_ms(1)

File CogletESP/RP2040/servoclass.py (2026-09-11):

from machine import Pin, I2C
import time


def clamp(x, a, b):
    return a if x < a else (b if x > b else x)


# ============================================================
# PCB V2.0 hardware configuration - checked against CogletESPV2.0 PDF
# ============================================================

PCA_ADDR = 0x40

# RP2040 -> PCA9685
PWM_SDA_PIN = 6
PWM_SCL_PIN = 7
PWM_NOE_PIN = 8

# GPIO6/7/8 are still taken directly from the PCB 2.0 schematic.

# Physical servo connector semantics.
#
# The number printed beside each PCB servo socket is the Socket ID, and the
# Socket ID is the PCA9685 channel number.  There is intentionally no second
# remapping table here:
#
#   Socket 0  -> PCA CH0   (Right Ear / EAR)
#   Socket 1  -> PCA CH1   (Left Ear / EAL)
#   Socket 2  -> PCA CH2   (Eyelid / LID)
#   Socket 3  -> PCA CH3   (Mouth / MOU)
#   Socket 4  -> PCA CH4   (Left Eye / EYL)
#   Socket 5  -> PCA CH5   (Right Eye / EYR)
#   Socket 8  -> PCA CH8   (Neck Pitch / PIT)
#   Socket 9  -> PCA CH9   (Neck Roll / ROL)
#   Socket 10 -> PCA CH10  (Base Yaw / YAW)
#
# Sockets 6, 7 and 11 remain valid physical/PCA channels even though they are
# not assigned to one of the named servos above.
SERVO_SOCKET_MIN = 0
SERVO_SOCKET_MAX = 11


# PCA9685 nOE is active LOW.
# Keep outputs disabled while modules are importing and pulses are preloaded.
_oe = Pin(PWM_NOE_PIN, Pin.OUT)
_oe.value(1)

_i2c = I2C(
    1,
    sda=Pin(PWM_SDA_PIN),
    scl=Pin(PWM_SCL_PIN),
    freq=400000,
)


class _PCA9685:
    MODE1 = 0x00
    MODE2 = 0x01
    LED0_ON_L = 0x06
    PRESCALE = 0xFE

    def __init__(self, i2c, address=0x40):
        self.i2c = i2c
        self.address = address
        self.freq = 50.0

    def _write8(self, reg, value):
        self.i2c.writeto_mem(
            self.address,
            reg,
            bytes((value & 0xFF,))
        )

    def _read8(self, reg):
        return self.i2c.readfrom_mem(
            self.address,
            reg,
            1
        )[0]

    def set_freq(self, freq):
        self.freq = float(freq)

        prescale = int(
            25000000.0 / (4096.0 * self.freq)
            - 1.0
            + 0.5
        )

        old_mode = self._read8(self.MODE1)

        # Sleep before changing PRESCALE.
        self._write8(
            self.MODE1,
            (old_mode & 0x7F) | 0x10
        )

        self._write8(self.PRESCALE, prescale)

        # Wake.
        self._write8(
            self.MODE1,
            old_mode & ~0x10
        )

        time.sleep_ms(5)

        # RESTART + AUTO-INCREMENT + ALLCALL.
        self._write8(
            self.MODE1,
            (old_mode & ~0x10) | 0xA1
        )

        # Totem-pole output driver.
        self._write8(self.MODE2, 0x04)

    def set_pwm(self, channel, on, off):
        reg = self.LED0_ON_L + channel * 4

        data = bytes((
            on & 0xFF,
            (on >> 8) & 0x0F,
            off & 0xFF,
            (off >> 8) & 0x0F,
        ))

        self.i2c.writeto_mem(
            self.address,
            reg,
            data
        )

    def write_us(self, channel, pulse_us):
        pulse_us = clamp(
            float(pulse_us),
            500.0,
            2500.0
        )

        counts = int(
            pulse_us
            * 4096.0
            * self.freq
            / 1000000.0
            + 0.5
        )

        counts = int(clamp(counts, 0, 4095))
        self.set_pwm(channel, 0, counts)


_pca = _PCA9685(_i2c, PCA_ADDR)
_ready = False

try:
    devices = _i2c.scan()

    print(
        "[PCB2] I2C1 scan:",
        ["0x{:02X}".format(x) for x in devices]
    )

    if PCA_ADDR in devices:
        _pca.set_freq(50)
        _ready = True
        print("[PCB2] PCA9685 OK: address 0x40, 50 Hz")
    else:
        print("[PCB2] ERROR: PCA9685 0x40 NOT FOUND")

except Exception as exc:
    print("[PCB2] PCA9685 init failed:", exc)
    _ready = False


def is_ready():
    return _ready


def enable_outputs():
    if not _ready:
        print("[PCB2] Refuse enable: PCA9685 is not ready")
        return False

    # Active-low nOE.
    _oe.value(0)
    print("[PCB2] GPIO8 PWM_nOE = 0 -> servo outputs ENABLED")
    return True


def disable_outputs():
    _oe.value(1)
    print("[PCB2] GPIO8 PWM_nOE = 1 -> servo outputs DISABLED")


class Servo:
    def __init__(
        self,
        pin_num,
        max_speed=120.0,
        max_accel=360.0,
        min_angle=0.0,
        max_angle=180.0,
        enabled=True
    ):
        # pin_num is the physical PCB Socket ID printed on the board.
        # By hardware definition, Socket ID == PCA9685 channel.
        self.port_num = int(pin_num)

        if not (SERVO_SOCKET_MIN <= self.port_num <= SERVO_SOCKET_MAX):
            raise ValueError(
                "Invalid PCB servo Socket ID: {} (expected {}..{})".format(
                    self.port_num,
                    SERVO_SOCKET_MIN,
                    SERVO_SOCKET_MAX,
                )
            )

        self.channel = self.port_num

        # motion state - same as V1
        self.pos = 90.0
        self.vel = 0.0
        self.target = 90.0

        # tuning - same as V1
        self.max_speed = float(max_speed)
        self.max_accel = float(max_accel)

        # limits - same as V1
        self.min_angle = float(min_angle)
        self.max_angle = float(max_angle)

        self.pos_tolerance = 0.6
        self.vel_tolerance = 1.0

        self.enabled = enabled

        # Preload 90 degrees while nOE remains disabled.
        self._write_pwm(self.pos)

        print(
            "[PCB2] SOCKET{} -> PCA CH{}".format(
                self.port_num,
                self.channel
            )
        )

    def set_target(self, angle):
        self.target = clamp(
            float(angle),
            self.min_angle,
            self.max_angle
        )

    def set_immediate(self, angle):
        """
        Write a servo position immediately, bypassing speed/acceleration
        interpolation while keeping pos/target/vel synchronized.
        """
        angle = clamp(
            float(angle),
            self.min_angle,
            self.max_angle
        )

        self.pos = angle
        self.target = angle
        self.vel = 0.0
        self._write_pwm(angle)

    def update(self, dt):
        if not self.enabled:
            return

        if dt <= 0:
            return

        error = self.target - self.pos
        dist = abs(error)

        desired_dir = (
            0
            if dist < 1e-9
            else (1.0 if error > 0 else -1.0)
        )

        if abs(self.vel) < 1e-9:
            vel_dir = 0.0
        else:
            vel_dir = (
                1.0 if self.vel > 0 else -1.0
            )

        if (
            dist <= self.pos_tolerance
            and abs(self.vel) <= self.vel_tolerance
        ):
            self.pos = self.target
            self.vel = 0.0
            self._write_pwm(self.pos)
            return
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

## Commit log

2026-02-25 added PCB
2026-02-25 added version B32 printfiles
2026-03-03 updated 3d print Files
2026-03-10 added missing part to printfile
